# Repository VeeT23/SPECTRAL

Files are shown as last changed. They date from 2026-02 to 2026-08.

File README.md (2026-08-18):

# SPECTRAL

Short description of the embedded system and what it does.

## Overview

SPECTRAL is a performance line following robot 

## Hardware

### Main Components

| Component | Part Number | Description |
| --- | --- | --- |
| MCU | ESP32-WROOM-32UE  | Main microcontroller |
| Orientation Sensor | BNO055 | 9-DoF absolute orientation sensor with accelerometer, gyroscope, and magnetometer |
| Motor Controller | ODrive Micro | 100 W BLDC motor controller |
| Motor | Flash Hobby D4215 | 4215 650 KV BLDC motor, 3S–6S |
| CAN Transceiver | ATA6561 | CAN transceiver for motor controller communication |

### Pinout

## Pin Definitions

| GPIO | Function | Interface | Notes |
| ---: | --- | --- | --- |
| 16 | A0 | Sensor Address | Sensor address select |
| 17 | A1 | Sensor Address | Sensor address select |
| 18 | A2 | Sensor Address | Sensor address select |
| 32 | S0 | Sensor Output  | Sensor output |
| 33 | S1 | Sensor Output  | Sensor output |
| 34 | S2 | Sensor Output  | Sensor output |
| 35 | S3 | Sensor Output  | Sensor output |
| 39 | S4 | Sensor Output  | Sensor output |
| 19 | CAN_STBY | CAN | CAN transceiver standby control |
| 4 | CAN_RX | CAN | CAN receive |
| 5 | CAN_TX | CAN | CAN transmit |
| 22 | SDA | I2C | I2C data |
| 21 | SCL | I2C | I2C clock |
| 25 | BUZZER | GPIO | Buzzer control |
| 26 | NEOPIXEL | GPIO | Exposed on board; currently unused |
| 27 | FAN_PWM  | PWM | Exposed on board; currently unused |

## Software

### Toolchain

- **Platform:** Espressif32
- **MCU:** ESP32-WROOM-32UE
- **Framework:** Arduino
- **Build System:** PlatformIO
- **IDE:** Visual Studio Code + PlatformIO

## Repository Structure

```text
SPECTRAL/
├── firmware/
│   ├── common/
│   ├── control_station_firmware/
│   └── spectral_firmware/
├── hardware/
│   ├── main_board/
│   ├── power_module/
│   └── sensor_module/
├── .gitignore
└── README.md
```

## Configuration

| Parameter | Value | Description |
| --- | ---: | --- |
| Control Frequency | 1000 Hz | Main control loop frequency |
| Display Update Period | 40 ms | Period between display updates |
| Wheel Spacing | 104 mm | Distance between drive wheels |
| Wheel Diameter | 60 mm | Drive wheel diameter |
| Wheel Circumference | 0.1885 m | Calculated wheel circumference |
| Line Following Kp | 1.0 | Proportional gain |
| Line Following Ki | 0.01 | Integral gain |
| Line Following Kd | 0.01 | Derivative gain |
| Number of Sensor Modules | 5 | Number of IR sensor modules |
| Sensors per Module | 8 | Number of sensors on each module |
| Total IR Sensors | 40 | Total number of IR sensors |
| IR Threshold | 2000 | Sensor threshold used for line detection |
| Controller MAC | `D8:3B:DA:46:57:80` | MAC address of the remote controller |
| Radio RX Timeout | 1000 ms | Maximum time without receiving controller data |
| Telemetry Frequency | 120 Hz | Telemetry transmission frequency |
| Radio Debug | Disabled | Enables/disables radio debug output |
| CAN Bitrate | 500 kbit/s | CAN bus communication speed |
| CAN TX Timeout | 40 ms | Maximum time to wait for CAN transmission |
| Serial Baud Rate | 115200 | Serial communication baud rate |
| ODrive Heartbeat Timeout | 200 ms | Maximum time without receiving an ODrive heartbeat |
| Motors Enabled | Yes | Enables motor operation |

### ODrive Commands

The following CAN command IDs are used to communicate with the ODrive motor controller:

| Command | CAN ID | Description |
| --- | -----: | --- |
| Heartbeat | `0x01` | ODrive heartbeat |
| Emergency Stop | `0x02` | Trigger emergency stop |
| Set Axis State | `0x07` | Change ODrive axis state |
| Get Encoder Estimate | `0x09` | Request encoder position/velocity estimate |
| Set Input Velocity | `0x0D` | Set motor velocity command |
| Clear Errors | `0x18` | Clear ODrive errors |

### ODrive Axis States

| State | Value | Description |
| --- | ----: | --- |
| Idle | `1` | Motor disabled / idle |
| Closed Loop | `8` | Motor enabled for closed-loop control |

## Power

Spectral uses a 450 mAh 3s 75C lipo
Running power is unknown however the circuit supports up to 10A continous.
Idle power is measured to be ~140ma

WARNING: AS IT STANDS CURRENTLY, SPECTRAL LACKS OVER DISCHARGE PROTECTION, MONITOR BATTERY VOLTAGE BETWEEN RUNS TO AVOID DAMAGE TO THE BATTERY

## Communication

* UART - Serial debugging/flashing
* I2C - Display screen
* CAN - Motor controllers
* ESP-NOW - Base station communication

## Known Issues

* Dynamic velocity control has no smoothing between setpoints
* Power module lacks battery monitoring for undervoltage

## Future Work

This project is closed, however I will add documentation/clean up issues on request. 

## License

This project is licensed under the GNU GENERAL PUBLIC LICENSE.

## Author

**Veronica Tobias**

[GitHub](https://github.com/VeeT23)

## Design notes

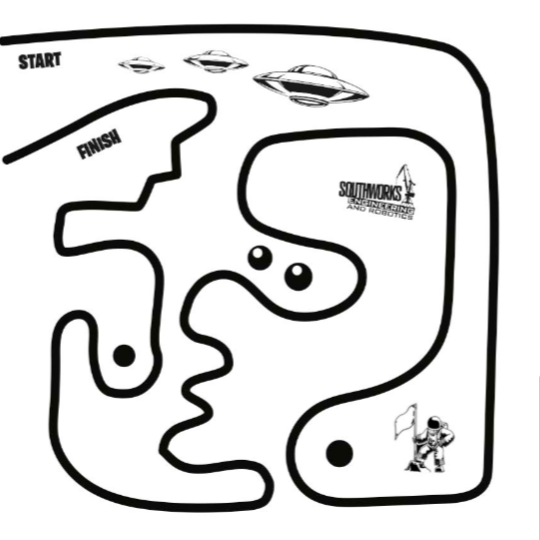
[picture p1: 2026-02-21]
spectral_data_analysis/pathfinder_2026.png

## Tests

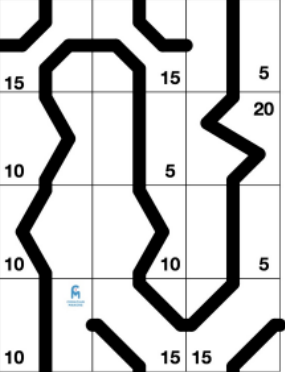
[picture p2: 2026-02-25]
spectral_data_analysis/test.png

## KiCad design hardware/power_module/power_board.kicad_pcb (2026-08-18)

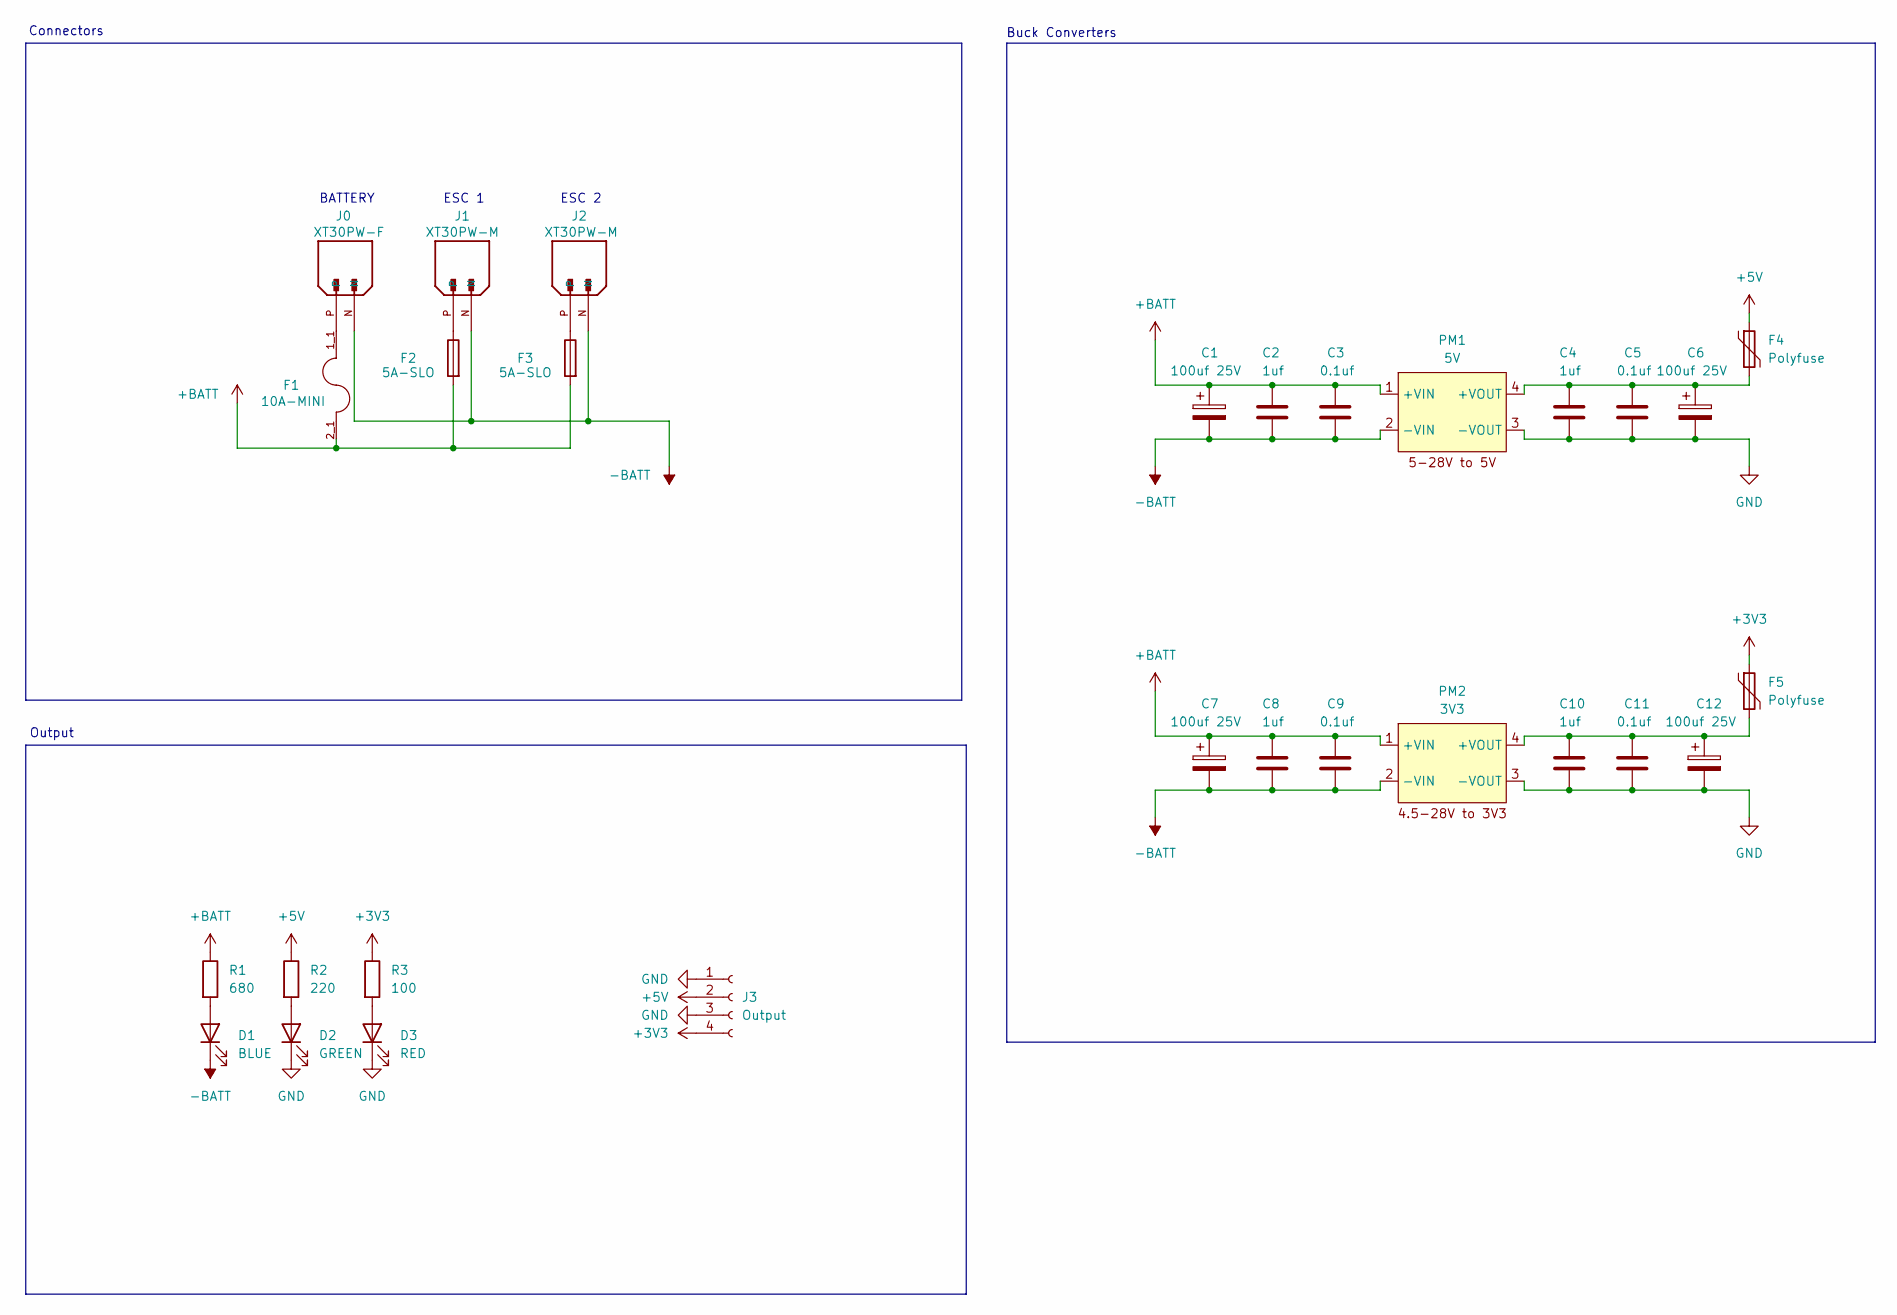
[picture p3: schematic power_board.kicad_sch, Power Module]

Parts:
C1, C6, C7, C12: 100uf 25V; CP_Radial_D5.0mm_P2.00mm
C2, C4, C8, C10: 1uf; C_0603_1608Metric_Pad1.08x0.95mm_HandSolder
C3, C5, C9, C11: 0.1uf; C_0603_1608Metric_Pad1.08x0.95mm_HandSolder
D1: BLUE; LED_0603_1608Metric_Pad1.05x0.95mm_HandSolder
D2: GREEN; LED_0603_1608Metric_Pad1.05x0.95mm_HandSolder
D3: RED; LED_0603_1608Metric_Pad1.05x0.95mm_HandSolder
F1: 10A-MINI; FUSE_3549-2; PARTREV D; DigiKey_Part_Number 36-3549-2-ND
F2, F3: 5A-SLO; Fuse_1206_3216Metric_Pad1.42x1.75mm_HandSolder
F4, F5: Polyfuse; Fuse_2920_7451Metric_Pad2.10x5.45mm_HandSolder
J0: XT30PW-F; AMASS_XT30PW-M; PARTREV 1.2
J1, J2: XT30PW-M; AMASS_XT30PW-M; PARTREV 1.2
J3: Output; JST_GH_BM04B-GHS-TBT_1x04-1MP_P1.25mm_Vertical
PM1: 5V; DC_Buck_Module
PM2: 3V3; DC_Buck_Module
R1: 680; R_0603_1608Metric_Pad0.98x0.95mm_HandSolder
R2: 220; R_0603_1608Metric_Pad0.98x0.95mm_HandSolder
R3: 100; R_0603_1608Metric_Pad0.98x0.95mm_HandSolder

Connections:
+3V3: F5.1, J3.4, R3.1
+5V: F4.1, J3.2, R2.1
+BATT: C1.1, C2.1, C3.1, C7.1, C8.1, C9.1, F1.2_1, F1.2_2, F2.2, F3.2, PM1.1 (+VIN), PM2.1 (+VIN), R1.1
-BATT: C1.2, C2.2, C3.2, C7.2, C8.2, C9.2, D1.1 (K), J0.N, J0.S1, J0.S2, J1.N, J1.S1, J1.S2, J2.N, J2.S1, J2.S2, PM1.2 (-VIN), PM2.2 (-VIN)
GND: C4.2, C5.2, C6.2, C10.2, C11.2, C12.2, D2.1 (K), D3.1 (K), J3.1, J3.3, J3.MP, PM1.3 (-VOUT), PM2.3 (-VOUT)
unnamed: D1.2 (A), R1.2
unnamed: D2.2 (A), R2.2
unnamed: D3.2 (A), R3.2
unnamed: F1.1_1, F1.1_2, J0.P
unnamed: F2.1, J1.P
unnamed: F3.1, J2.P
unnamed: C4.1, C5.1, C6.1, F4.2, PM1.4 (+VOUT)
unnamed: C10.1, C11.1, C12.1, F5.2, PM2.4 (+VOUT)

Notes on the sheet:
BATTERY
Connectors
ESC 1
ESC 2
Buck Converters
Output

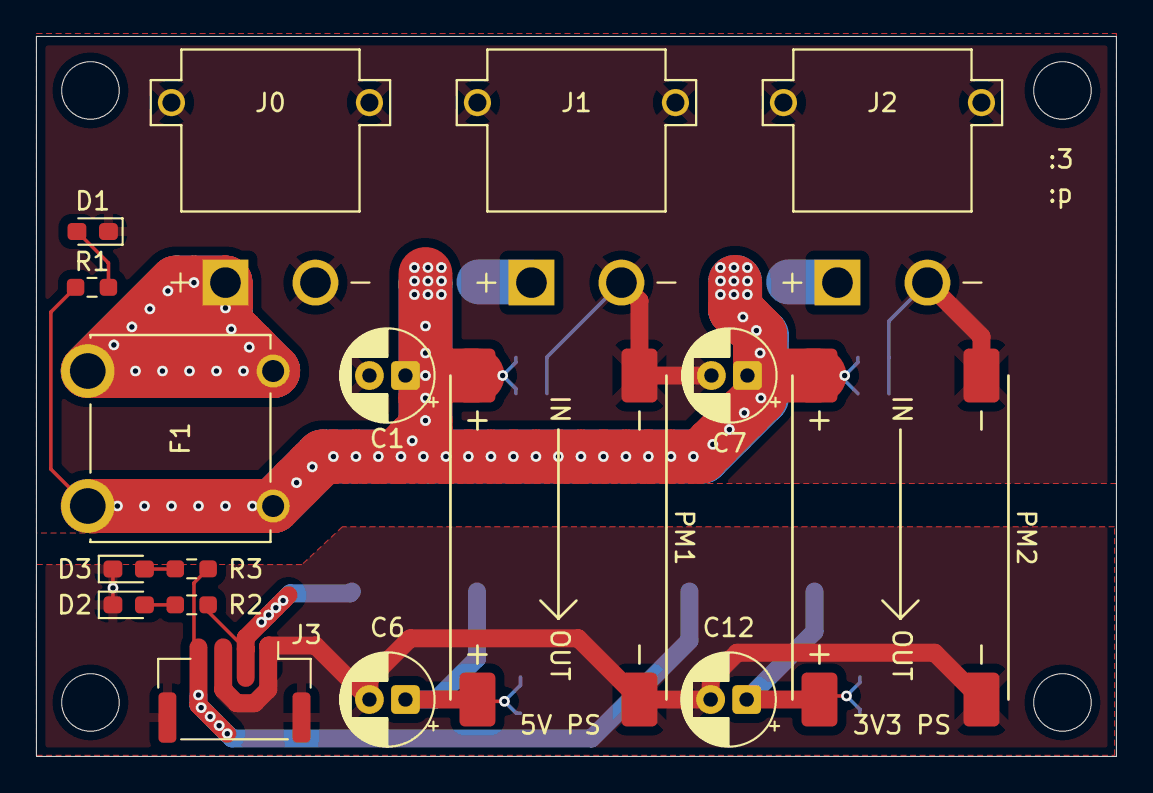
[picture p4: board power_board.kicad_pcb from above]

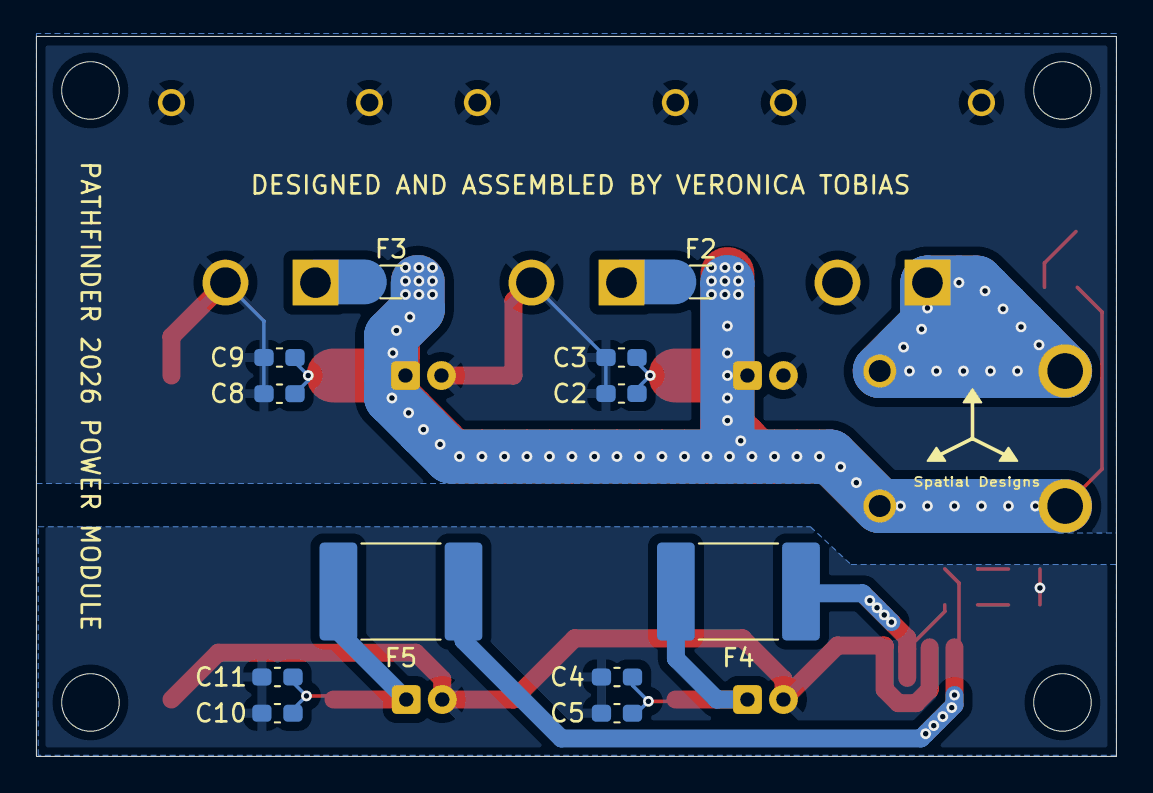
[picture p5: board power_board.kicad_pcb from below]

Board: 2 copper layers, 60.0 x 40.0 mm, 29 parts (12 on the bottom side), 13 nets.

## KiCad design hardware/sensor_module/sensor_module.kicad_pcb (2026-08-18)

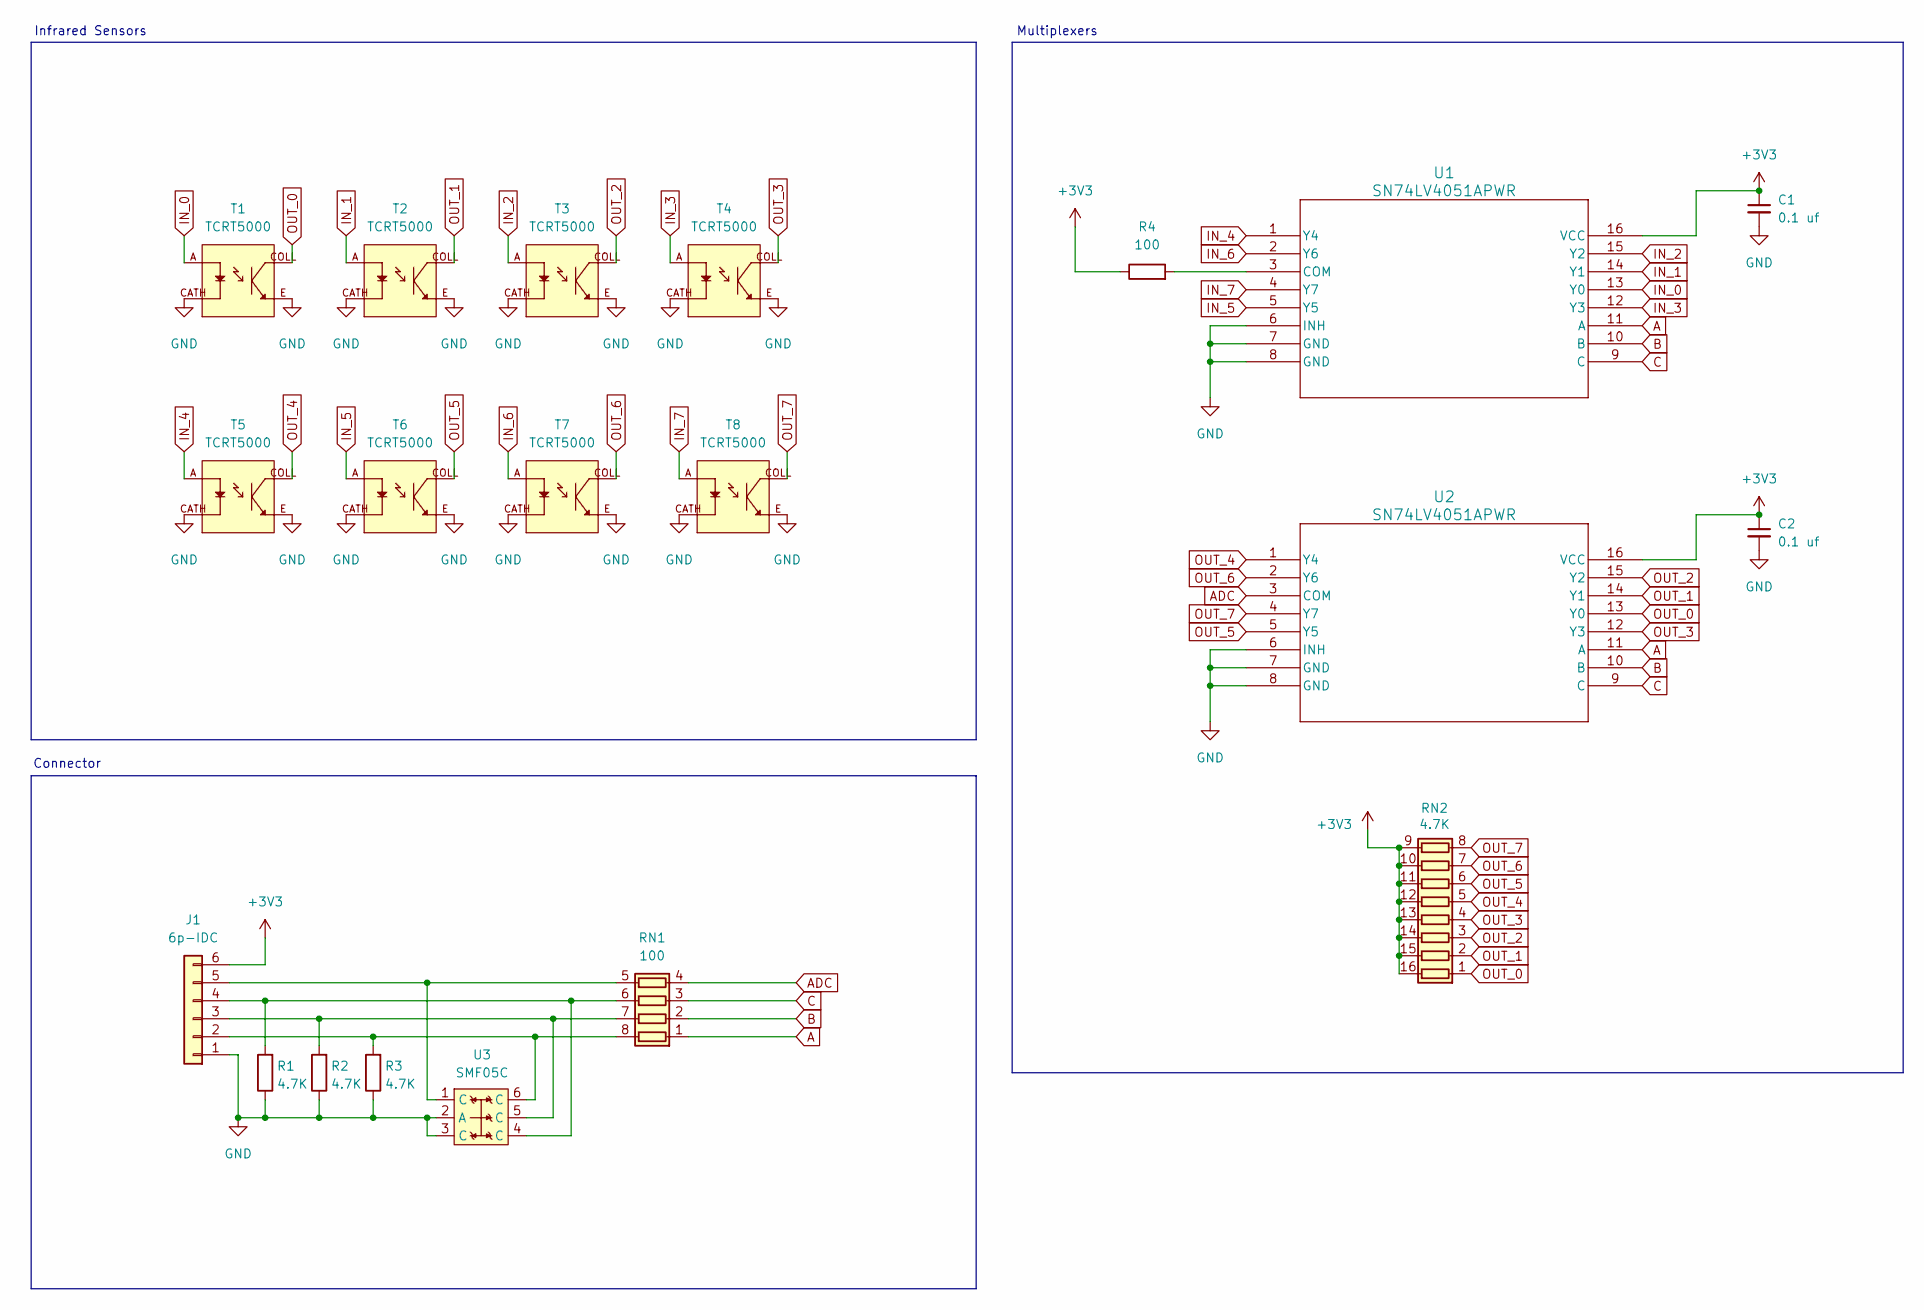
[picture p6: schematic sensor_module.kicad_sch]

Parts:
C1, C2: 0.1 uf; C_0603_1608Metric_Pad1.08x0.95mm_HandSolder
J1: 6p-IDC; CONN_SM06B-GHS-TB_JST
R1, R2, R3: 4.7K; R_0603_1608Metric_Pad0.98x0.95mm_HandSolder
R4: 100; R_0603_1608Metric_Pad0.98x0.95mm_HandSolder
RN1: 100; EXB28V_PAN-L
RN2: 4.7K; RES_EXB2HV
T1, T2, T3, T4, T5, T6, T7, T8: TCRT5000; TCRT5000-MINI; PARTREV 1.7
U1, U2: SN74LV4051APWR; PW16
U3: SMF05C; SOT-363_SC-70-6_Handsoldering

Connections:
+3V3: C1.1, C2.1, J1.6, R4.1, RN2.9 (R8.2), RN2.10 (R7.2), RN2.11 (R6.2), RN2.12 (R5.2), RN2.13 (R4.2), RN2.14 (R3.2), RN2.15 (R2.2), RN2.16 (R1.2), U1.16 (VCC), U2.16 (VCC)
A: RN1.1 (R1.1), U1.11 (A), U2.11 (A)
ADC: RN1.4 (R4.1), U2.3 (COM)
B: RN1.2 (R2.1), U1.10 (B), U2.10 (B)
C: RN1.3 (R3.1), U1.9 (C), U2.9 (C)
GND: C1.2, C2.2, J1.1, R1.1, R2.1, R3.1, T1.CATH, T1.E, T2.CATH, T2.E, T3.CATH, T3.E, T4.CATH, T4.E, T5.CATH, T5.E, T6.CATH, T6.E, T7.CATH, T7.E, T8.CATH, T8.E, U1.6 (INH), U1.7 (GND), U1.8 (GND), U2.6 (INH), U2.7 (GND), U2.8 (GND), U3.2 (A), U3.3 (C)
IN_0: T1.A, U1.13 (Y0)
IN_1: T2.A, U1.14 (Y1)
IN_2: T3.A, U1.15 (Y2)
IN_3: T4.A, U1.12 (Y3)
IN_4: T5.A, U1.1 (Y4)
IN_5: T6.A, U1.5 (Y5)
IN_6: T7.A, U1.2 (Y6)
IN_7: T8.A, U1.4 (Y7)
unnamed: J1.2, R3.2, RN1.8 (R1.2), U3.6 (C)
unnamed: J1.3, R2.2, RN1.7 (R2.2), U3.5 (C)
unnamed: J1.4, R1.2, RN1.6 (R3.2), U3.4 (C)
unnamed: J1.5, RN1.5 (R4.2), U3.1 (C)
unnamed: R4.2, U1.3 (COM)
OUT_0: RN2.1 (R1.1), T1.COLL, U2.13 (Y0)
OUT_1: RN2.2 (R2.1), T2.COLL, U2.14 (Y1)
OUT_2: RN2.3 (R3.1), T3.COLL, U2.15 (Y2)
OUT_3: RN2.4 (R4.1), T4.COLL, U2.12 (Y3)
OUT_4: RN2.5 (R5.1), T5.COLL, U2.1 (Y4)
OUT_5: RN2.6 (R6.1), T6.COLL, U2.5 (Y5)
OUT_6: RN2.7 (R7.1), T7.COLL, U2.2 (Y6)
OUT_7: RN2.8 (R8.1), T8.COLL, U2.4 (Y7)

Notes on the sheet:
Infrared Sensors
Connector
Multiplexers

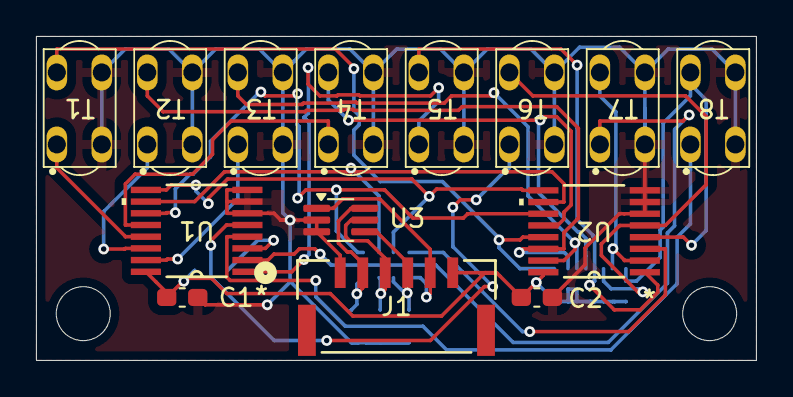
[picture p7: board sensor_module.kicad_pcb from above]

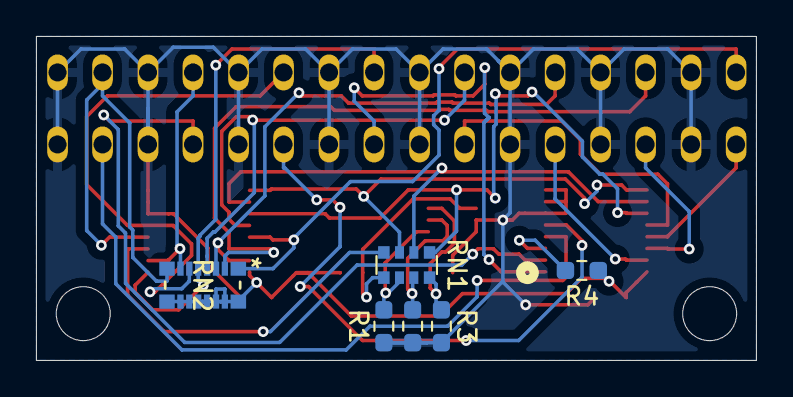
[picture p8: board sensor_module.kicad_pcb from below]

Board: 2 copper layers, 40.0 x 18.0 mm, 20 parts (6 on the bottom side), 27 nets.

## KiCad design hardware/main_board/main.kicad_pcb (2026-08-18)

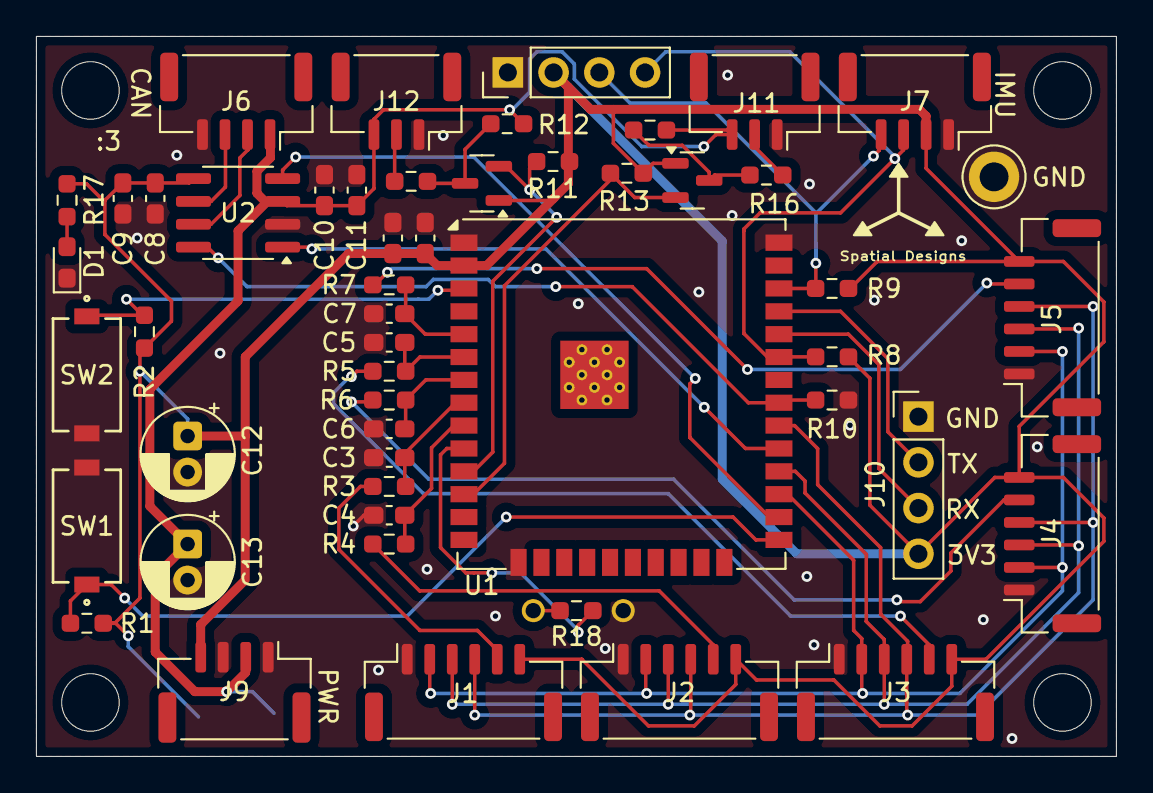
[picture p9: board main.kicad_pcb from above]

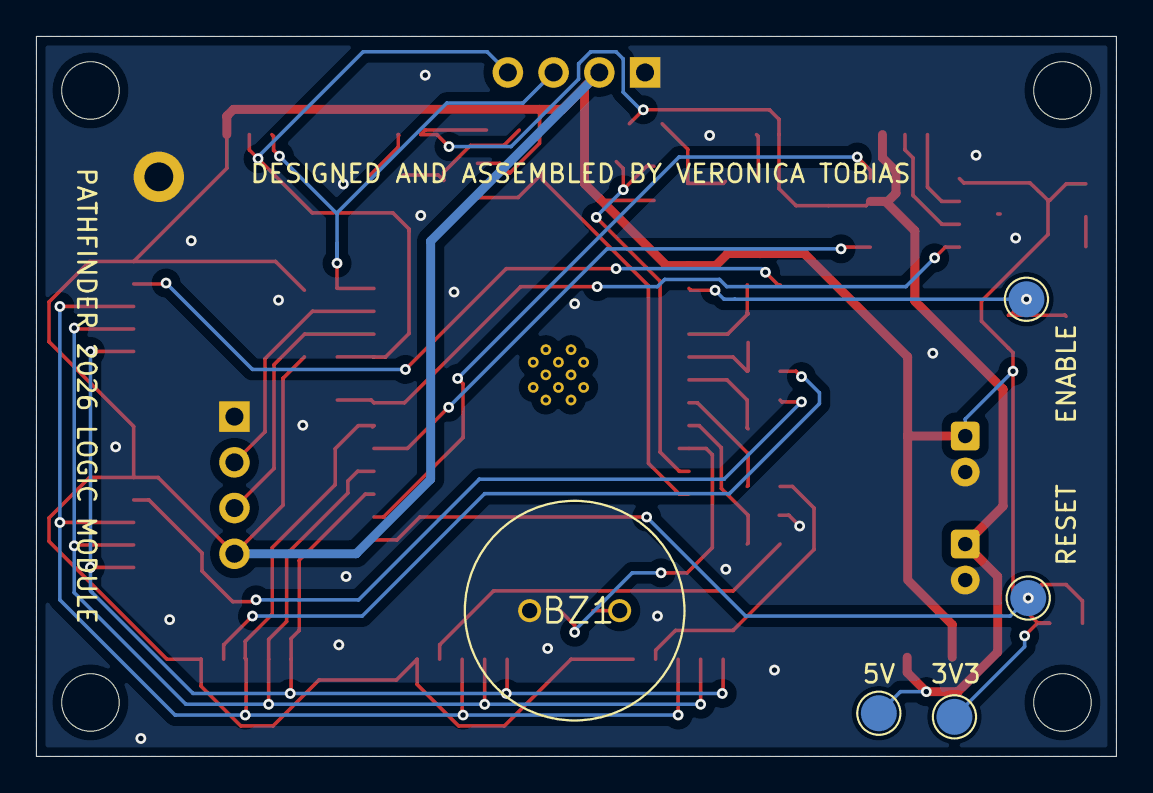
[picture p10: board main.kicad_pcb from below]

Board: 2 copper layers, 60.0 x 40.0 mm, 56 parts (5 on the bottom side), 36 nets.

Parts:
BZ1: Buzzer; XDCR_PS1240P02CT3
C1, C8, C10: 0.1uf; C_0603_1608Metric_Pad1.08x0.95mm_HandSolder
C2, C9, C11: 10uf; C_0603_1608Metric_Pad1.08x0.95mm_HandSolder
C3, C4, C5, C6, C7: 1nf; C_0603_1608Metric_Pad1.08x0.95mm_HandSolder
C12, C13: 100uf; CP_Radial_D5.0mm_P2.00mm
D1: RED; LED_0603_1608Metric_Pad1.05x0.95mm_HandSolder
J1: Sensor 1; JST_GH_SM06B-GHS-TB_1x06-1MP_P1.25mm_Horizontal
J2: Sensor 2; JST_GH_SM06B-GHS-TB_1x06-1MP_P1.25mm_Horizontal
J3: Sensor 3; JST_GH_SM06B-GHS-TB_1x06-1MP_P1.25mm_Horizontal
J4: Sensor 4; JST_GH_SM06B-GHS-TB_1x06-1MP_P1.25mm_Horizontal
J5: Sensor 5; JST_GH_SM06B-GHS-TB_1x06-1MP_P1.25mm_Horizontal
J6: CAN; JST_GH_SM04B-GHS-TB_1x04-1MP_P1.25mm_Horizontal
J7: IMU; JST_GH_SM04B-GHS-TB_1x04-1MP_P1.25mm_Horizontal
J8: OLED; PinHeader_1x04_P2.54mm_Vertical
J9: Power; JST_GH_BM04B-GHS-TBT_1x04-1MP_P1.25mm_Vertical
J10: UART; PinHeader_1x04_P2.54mm_Vertical
J11: PWM; JST_GH_SM03B-GHS-TB_1x03-1MP_P1.25mm_Horizontal
J12: NEOPIXEL; JST_GH_SM03B-GHS-TB_1x03-1MP_P1.25mm_Horizontal
Q1, Q4: BSS138; SOT-23
R1, R2, R8, R9, R10, R11, R12, R13, R14: 4.7K; R_0603_1608Metric_Pad0.98x0.95mm_HandSolder
R3, R4, R5, R6, R7, R15, R16, R17, R18: 100; R_0603_1608Metric_Pad0.98x0.95mm_HandSolder
SW1: BOOT; SW_PTS636_CNK
SW2: RESET; SW_PTS636_CNK
TP1: BOOT; TestPoint_Pad_D2.0mm
TP2: EN; TestPoint_Pad_D2.0mm
TP3: 3V3; TestPoint_Pad_D2.0mm
TP4: 5V; TestPoint_Pad_D2.0mm
TP5: GND; TestPoint_Keystone_5005-5009_Compact
U1: ESP32-WROOM-32UE_M113EH6400UH3Q0_; ESP32-WROOM-32UE
U2: ATA6561-GAQW-N; SOIC-8_3.9x4.9mm_P1.27mm

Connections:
+3V3: C1.1, C2.1, C8.1, C9.1, C12.1, J1.6, J2.6, J3.6, J4.6, J5.6, J7.2, J8.2, J9.4, J10.4, Q1.1 (G), Q4.1 (G), R1.1, R2.1, R8.2, R9.2, R11.2, R13.2, R17.1, TP3.1, U1.2 (3V3), U2.5 (VRXD)
+5V: C10.1, C11.1, C13.1, J6.1, J9.2, J11.3, J12.3, R12.2, R14.2, TP4.1, U2.3 (VCC)
A0: J1.2, J2.2, J3.2, J4.2, J5.2, U1.27 (IO16)
A1: J1.3, J2.3, J3.3, J4.3, J5.3, U1.28 (IO17)
A2: J1.4, J2.4, J3.4, J4.4, J5.4, U1.30 (IO18)
BOOT: R1.2, SW1.1, TP1.1, U1.25 (IO0)
BUZZER: R18.1, U1.10 (IO25)
CAN_RX: U1.26 (IO4), U2.4 (RXD)
CAN_STBY: R10.1, U1.31 (IO19), U2.8 (S)
CAN_TX: U1.29 (IO5), U2.1 (TXD)
EN: R2.2, SW2.1, TP2.1, U1.3 (EN)
GND: BZ1.2 (-), C1.2, C2.2, C3.2, C4.2, C5.2, C6.2, C7.2, C8.2, C9.2, C10.2, C11.2, C12.2, C13.2, D1.1 (K), J1.1, J2.1, J3.1, J4.1, J5.1, J6.4, J7.1, J8.1, J9.1, J9.3, J10.1, J11.1, J12.1, R10.2, SW1.2, SW2.2, TP5.1, U1.1 (GND), U1.15 (GND), U1.38 (GND), U2.2 (GND)
NEO: Q4.2 (S), R11.1, U1.11 (IO26)
unnamed: BZ1.1 (+), R18.2
unnamed: D1.2 (A), R17.2
unnamed: J6.2, U2.7 (CANH)
unnamed: J6.3, U2.6 (CANL)
unnamed: J11.2, R16.2
unnamed: J12.2, R15.2
unnamed: Q1.3 (D), R14.1, R16.1
unnamed: Q4.3 (D), R12.1, R15.1
unnamed: C3.1, R3.2, U1.8 (IO32)
unnamed: C4.1, R4.2, U1.9 (IO33)
unnamed: C5.1, R5.1, U1.6 (IO34)
unnamed: C6.1, R6.1, U1.7 (IO35)
unnamed: C7.1, R7.1, U1.5 (SENSOR_VN)
PWM: Q1.2 (S), R13.1, U1.12 (IO27)
RX: J10.3, U1.34 (RXD0)
S0: J1.5, R3.1
S1: J2.5, R4.1
S2: J3.5, R5.2
S3: J4.5, R6.2
S4: J5.5, R7.2
SCL: J7.4, J8.3, R9.1, U1.36 (IO22)
SDA: J7.3, J8.4, R8.1, U1.33 (IO21)
TX: J10.2, U1.35 (TXD0)

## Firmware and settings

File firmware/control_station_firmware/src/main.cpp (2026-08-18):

#include <Arduino.h>
#include <Wire.h>

#include "screen.h"
#include "joystick.h"
#include "pin_def.h"
#include "config.h"
#include "radio.h"
#include "packet.h"

// ================= INPUT DEVICES ===============

Joystick joy_left(
    PINS::JOY_LEFT::X,
    PINS::JOY_LEFT::Y,
    PINS::JOY_LEFT::BUTTON,
    true,
    false);

Joystick joy_right(
    PINS::JOY_RIGHT::X,
    PINS::JOY_RIGHT::Y,
    PINS::JOY_RIGHT::BUTTON,
    false,
    true);

// ================= RADIO =======================

using ControllerRadio = ESPNowRadio<ControlPacket, TelemetryPacket>;
ControllerRadio &radio = ControllerRadio::instance();

// ================= SETUP =======================

void setup()
{
    delay(2000);
    Serial.begin(576000);

    Wire.begin();

    Screen::instance().init(0x3C);
    if (!radio.begin(ROBOT_MAC, RX_TIMEOUT_MS, RADIO_DEBUG))
    {
        while (true)
        {
            delay(1000);
        }
    }
}

// ================= LOOP ========================

void loop()
{

    joy_left.poll();
    joy_right.poll();

    static uint32_t lastSend = 0;
    static uint8_t control_mode = 0;           // 0: IDLE, 1: MANUAL, 2: AUTO
    static float max_velocity = BASE_VELOCITY; // Default max velocity, can be adjusted in AUTO mode
    static bool in_config_menu = false;

    if (joy_left.just_released())
    {
        if (in_config_menu)
        {
            in_config_menu = false;
        }
        else
        {
            if (control_mode == 0) // Only allow config menu access from IDLE mode
            {
                in_config_menu = true;
            }
            else
            {
                control_mode = 0; // IDLE
            }
        }
    }

    if (joy_right.just_released())
    {
        if (in_config_menu)
        {
            // Exit config menu on right joystick button press
            in_config_menu = false;
        }
        else
        {
            // Cycle control modes on right joystick button press
            control_mode++;
            if (control_mode > 2)
                control_mode = 0;
        }
    }

    if (in_config_menu)
    {
        max_velocity += joy_right.y() * 0.005f;               // Adjust max velocity with right joystick up/down
        max_velocity = constrain(max_velocity, 0.05f, 10.0f); // Constrain to reasonable range
    }

    if (millis() - lastSend >= TX_PERIOD)
    {
        lastSend = millis();

        float throttle = joy_left.y() * max_velocity;                    // Forward/backward on left joystick
        float steering = joy_right.x() * (1 - abs(joy_left.y()) * 0.5f); // Left/right on right joystick

        float throttle_left, throttle_right;

        if (throttle == 0.0f && steering != 0.0f)
        {
            // In-place turning: wheels spin opposite directions
            throttle_left = steering * max_velocity;
            throttle_right = -steering * max_velocity;
        }
        else
        {
            // Normal turning: adjust throttle per wheel
            float turn_scale = steering * abs(throttle);
            throttle_left = throttle + turn_scale;
            throttle_right = throttle - turn_scale;
        }

        ControlPacket cmd{};
        cmd.control_mode = control_mode;
        cmd.throttle_left = throttle_left; // m/s
        cmd.throttle_right = throttle_right;
        cmd.max_velocity = max_velocity; // Only used in AUTO mode
        radio.send(cmd);
    }

    bool timeout = radio.update();

    TelemetryPacket pkt;

    if (radio.recieve(pkt))
    {
        if (Serial)
        {
            const uint16_t size = sizeof(pkt);

            Serial.write((uint8_t *)&TELEMETRY_HEADER, sizeof(TELEMETRY_HEADER));
            Serial.write((uint8_t *)&size, sizeof(size));
            Serial.write((uint8_t *)&pkt, size);
        }
    }

    // ---- UI ----
    auto &gfx = Screen::instance().gfx();
    gfx.clearDisplay();

    if (in_config_menu)
    {
        gfx.setTextSize(1);
        gfx.setCursor(0, 0);
        gfx.printf("Max Velocity: %.2f", max_velocity);
    }
    else
    {                // Default control menu
        if (timeout) // Prioritize showing timeout error over no serial error, since no serial may just mean "not plugged in yet"
        {
            Screen::instance().drawCenteredText("TIMEOUT", 0, 0, 128, 32, 2);
        }
        else
        {
            if (!Serial)
            {
                Screen::instance().drawCenteredText("NO SERIAL", 0, 0, 128, 32, 1);
            }
        }

        joy_left.draw(0, 32, 32, 32);
        joy_right.draw(96, 32, 32, 32);

        // Draw MODE label in top center box
        Screen::instance().drawCenteredText("MODE", 32, 32, 64, 16, 1);

        // Draw control mode value in bottom center box
        const char *mode_str = "";
        switch (control_mode)
        {
        case 0:
            mode_str = "IDLE";
            break;
        case 1:
            mode_str = "REMO";
            break;
        case 2:
            mode_str = "AUTO";
            break;
        }
        Screen::instance().drawCenteredText(mode_str, 32, 48, 64, 16, 2);
    }
    gfx.display();
    delay(10);
}

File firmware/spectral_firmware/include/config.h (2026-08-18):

#pragma once
#include <Arduino.h>

// ---------------- CONTROL ----------------
constexpr uint32_t CONTROL_HZ = 1000;
constexpr TickType_t CONTROL_PERIOD = pdMS_TO_TICKS(1000 / CONTROL_HZ);
constexpr TickType_t DRAW_PERIOD = pdMS_TO_TICKS(40);

constexpr uint8_t WHEEL_SPACING_MM = 104;
constexpr uint8_t WHEEL_DIAMETER_MM = 60;
constexpr float WHEEL_SPACING_M = WHEEL_SPACING_MM / 1000.0f;
constexpr float WHEEL_CIRCUMFERENCE_M =
    (WHEEL_DIAMETER_MM * PI) / 1000.0f;

constexpr float KP = 1.0f;  // Proportional gain for line following
constexpr float KI = 0.01f; // Integral gain for line following
constexpr float KD = 0.01f; // Derivative gain for line following

// ---------------- IR SENSORS ----------------
constexpr uint8_t NUM_MODULES = 5;
constexpr uint8_t SENSORS_PER_MODULE = 8;
constexpr uint8_t TOTAL_SENSORS = NUM_MODULES * SENSORS_PER_MODULE;
constexpr uint16_t IR_THRESHOLD = 2000; // Example threshold value

// ---------------- RADIO ----------------

const uint8_t CONTROLLER_MAC[6] = {0xD8, 0x3B, 0xDA, 0x46, 0x57, 0x80};
constexpr uint32_t RX_TIMEOUT_MS = 1000;
constexpr uint32_t TELEMETRY_FREQUENCY_HZ = 120;
constexpr TickType_t TELEMETRY_PERIOD = pdMS_TO_TICKS(1000 / TELEMETRY_FREQUENCY_HZ);
constexpr bool RADIO_DEBUG = false;

// ---------------- CAN ----------------
constexpr uint32_t CAN_BITRATE = 500000;
constexpr uint32_t CAN_TX_TIMEOUT_MS = 40;

// ---------------- SERIAL ----------------
constexpr uint32_t SERIAL_BAUD = 115200;

// ---------------- ODRIVE ----------------
constexpr uint32_t ODRIVE_CMD_HEARTBEAT = 0x01;
constexpr uint32_t ODRIVE_CMD_ESTOP = 0x02;
constexpr uint32_t ODRIVE_CMD_SET_AXIS_STATE = 0x07;
constexpr uint32_t ODRIVE_CMD_GET_ENCODER_EST = 0x09;
constexpr uint32_t ODRIVE_CMD_SET_INPUT_VEL = 0x0D;
constexpr uint32_t ODRIVE_CMD_CLEAR_ERRORS = 0x18;

constexpr uint32_t AXIS_STATE_CLOSED_LOOP = 8;
constexpr uint32_t AXIS_STATE_IDLE = 1;

constexpr uint32_t HEARTBEAT_TIMEOUT_MS = 200;

// ---------------- DEBUG ----------------
constexpr bool ENABLE_MOTORS = true;

// See radio for RADIO_DEBUG

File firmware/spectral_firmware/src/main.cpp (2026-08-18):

#include <Arduino.h>
#include "pin_def.h" // Pin configs
// Debug
#include "screen.h"
#include "buzzer.h"
// Peripherals
#include "global_state.h" //Holds radio + global data
#include "can_bus.h"
// Main loop
#include "control.h"

#include "splash.h"

/**
 * Main boot sequence
 * see global_state.h for config
 */

void setup()
{
    delay(100);
    // ---------- SERIAL INIT ----------
    Serial.begin(SERIAL_BAUD);
    Serial.println("Booting...");


    // ---------- CONFIGURE PINS ---------
    Serial.println("Configuring Pins...");
    PINS::configure_pins();
    

    // ---------- I2C INIT ----------
    Serial.println("Initializing I2C...");
    Wire.begin(PINS::SDA, PINS::SCL);
    Wire.setClock(400000);
    Wire.setTimeOut(5);

    // ---------- SCREEN INIT ----------
    Serial.println("Initializing OLED...");
    Screen::instance().init(0x3C);
    Screen::instance().gfx().clearDisplay();
    Screen::instance().gfx().drawBitmap(0, 0, SPLASH, 128, 64, SSD1306_WHITE);
    Screen::instance().gfx().display();

    // ---------- RADIO INIT ----------
    Serial.println("Initializing Radio...");
    auto& radio = RadioInstance();
    if (!radio.begin(CONTROLLER_MAC, RX_TIMEOUT_MS, RADIO_DEBUG)) {
        Serial.println("Radio init failed!");
        while (true) { delay(1000); }
    }

    // ---------- CAN INIT ----------
    Serial.println("Initializing CAN Bus...");
    if (!CANBus::instance().begin(PINS::CAN_TX, PINS::CAN_RX, CAN_BITRATE))
    {
        Serial.println("CAN init failed!");
        while (true) { delay(1000); }
    }
    if (CANBus::instance().test_can())
    {
        Serial.println("CAN TX failed!");
        while (true) { delay(1000); }
    }
    // ---------- BOOT FINISH ----------
    Serial.println("Boot sequence complete!");
    Buzzer::beep(2000,100);
    delay(2000);
    setup_control();
}

void loop()
{
    vTaskDelay(portMAX_DELAY);
}

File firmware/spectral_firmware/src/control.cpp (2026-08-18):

#include "control.h"
#include "pin_def.h"
#include "motor.h"
#include "screen.h"
#include "global_state.h"
#include "config.h"
#include "sensor_array.h"
#include "gyro.h"
#include "solution.h"

struct OdometryState
{
    float x = 0.0f;     // meters
    float y = 0.0f;     // meters
    float theta = 0.0f; // radians

    float distance = 0.0f; // total arc length traveled (meters)

    float prev_rev_L = 0.0f;
    float prev_rev_R = 0.0f;
};

inline void updateOdometry(
    OdometryState &state,
    float current_rev_L,
    float current_rev_R)
{
    // ---- Compute delta revolutions ----
    float delta_rev_L = current_rev_L - state.prev_rev_L;
    float delta_rev_R = current_rev_R - state.prev_rev_R;

    if (fabs(delta_rev_L) > 5 || fabs(delta_rev_R) > 5)
    {
        delta_rev_L = 0;
        delta_rev_R = 0;
    }

    state.prev_rev_L = current_rev_L;
    state.prev_rev_R = current_rev_R;

    // ---- Convert revolutions -> linear distance (meters) ----
    float dL = delta_rev_L * WHEEL_CIRCUMFERENCE_M;
    float dR = delta_rev_R * WHEEL_CIRCUMFERENCE_M;

    // ---- Differential drive kinematics ----
    float d = 0.5f * (dL + dR);                 // forward arc length

    // Accumulate arc length for distance traveled
    state.distance += d;
}

inline float wrapDegrees180(float angle_deg)
{
    while (angle_deg > 180.0f)
    {
        angle_deg -= 360.0f;
    }

    while (angle_deg <= -180.0f)
    {
        angle_deg += 360.0f;
    }

    return angle_deg;
}

inline float unwrapAngleNearReference(float angle_deg, float reference_deg)
{
    return reference_deg + wrapDegrees180(angle_deg - reference_deg);
}

inline bool hasReachedSolutionAngle(float previous_angle_deg, float target_angle_deg, float heading_deg)
{
    const float previous_unwrapped = unwrapAngleNearReference(previous_angle_deg, heading_deg);
    const float target_unwrapped = unwrapAngleNearReference(target_angle_deg, previous_unwrapped);

    if (target_unwrapped > previous_unwrapped)
    {
        return heading_deg >= target_unwrapped;
    }

    if (target_unwrapped < previous_unwrapped)
    {
        return heading_deg <= target_unwrapped;
    }

    return true;
}

inline bool isDistanceInSpan(float distance_m, const SolutionSpan &span)
{
    const float span_start = (span.start_distance < span.end_distance) ? span.start_distance : span.end_distance;
    const float span_end = (span.start_distance < span.end_distance) ? span.end_distance : span.start_distance;
    return distance_m >= span_start && distance_m <= span_end;
}

inline float getSpanPercentVelocityForDistance(const std::vector<SolutionSpan> &spans, float distance_m)
{
    for (size_t i = 0; i < spans.size(); ++i)
    {
        if (isDistanceInSpan(distance_m, spans[i]))
        {
            return spans[i].percent_velocity;
        }
    }

    return 1.0f;
}

inline void printSolutionDeserializeFailure(const char *label, const SolutionDeserializeDebugInfo &debug_info)
{
    Serial.printf(
        "Failed to decode %s: %s\n",
        label,
        solutionDeserializeErrorToString(debug_info.error));
    Serial.printf(
        "  data_len=%lu expected_len=%lu count=%lu failed_index=%lu\n",
        static_cast<unsigned long>(debug_info.data_length),
        static_cast<unsigned long>(debug_info.expected_length),
        static_cast<unsigned long>(debug_info.element_count),
        static_cast<unsigned long>(debug_info.failed_index));
    Serial.printf(
        "  magic=0x%08lX expected_magic=0x%08lX version=%lu expected_version=%lu\n",
        static_cast<unsigned long>(debug_info.actual_magic),
        static_cast<unsigned long>(debug_info.expected_magic),
        static_cast<unsigned long>(debug_info.actual_version),
        static_cast<unsigned long>(debug_info.expected_version));
}

inline void printDecodedSolutionSpans(const std::vector<SolutionSpan> &spans)
{
    Serial.println("Decoded solution spans:");
    for (size_t i = 0; i < spans.size(); ++i)
    {
        const SolutionSpan &span = spans[i];
        Serial.printf(
            "  [%u] start=%.3f end=%.3f speed=%.3f\n",
            static_cast<unsigned>(i),
            span.start_distance,
            span.end_distance,
            span.percent_velocity);
    }
}

// If odometry distance has exceeded a target point distance by this percent,
// we skip that target and jump to the next one.
constexpr float kSolutionDistanceJumpPercent = 1.0f;
constexpr float kMinLineFollowVelocityMps = 0.50f;

void controlTask(void *arg)
{
    // ---------- Task Scheduling -----------
    TickType_t lastWake = xTaskGetTickCount();
    TickType_t lastTelemetry = lastWake;
    TickType_t lastDraw = lastWake;
    TickType_t lastIdle = lastWake;
    TickType_t lastGyro = lastWake;
    TickType_t activeDuration = 0;
    
    // Gyro polling at 20Hz = 50ms period (reduced from 100Hz to avoid blocking)
    const TickType_t GYRO_PERIOD = pdMS_TO_TICKS(50);
    float gyro_yaw = 0.0f;
    float last_gyro_yaw = 0.0f;
    float relative_heading = 0.0f;
    bool has_gyro_yaw_sample = false;

    // ---------- Load Solution Points ----------
    std::vector<SolutionPoint> solution_points;
    std::vector<SolutionSpan> solution_spans;
    SolutionDeserializeDebugInfo point_decode_debug{};
    SolutionDeserializeDebugInfo span_decode_debug{};
    const bool points_loaded = deserializeEmbeddedSolutionPoints(solution_points, &point_decode_debug);
    const bool spans_loaded = deserializeEmbeddedSolutionSpans(solution_spans, &span_decode_debug);
    size_t next_solution_point_idx = 0;

    if (!points_loaded)
    {
        printSolutionDeserializeFailure("solution points", point_decode_debug);
        Serial.println("No valid solution points loaded; distance recalibration disabled");
    }
    else if (solution_points.empty())
    {
        Serial.println("Loaded solution points payload, but point count is 0; distance recalibration disabled");
    }
    else
    {
        relative_heading = solution_points.front().angle;
        next_solution_point_idx = (solution_points.size() > 1) ? 1 : solution_points.size();
        Serial.printf(
            "Loaded %u solution points; initial heading set to %.2f deg\n",
            static_cast<unsigned>(solution_points.size()),
            relative_heading);
    }

    if (!spans_loaded)
    {
        printSolutionDeserializeFailure("solution spans", span_decode_debug);
        Serial.println("No valid solution spans loaded; dynamic velocity scaling disabled");
    }
    else if (solution_spans.empty())
    {
        Serial.println("Loaded solution spans payload, but span count is 0; dynamic velocity scaling disabled");
    }
    else
    {
        Serial.printf(
            "Loaded %u solution spans for dynamic velocity scaling\n",
            static_cast<unsigned>(solution_spans.size()));
        printDecodedSolutionSpans(solution_spans);
    }

    // ---------- Initialize Gyro ----------
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

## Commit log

2026-01-21 Initial project structure and core modules
    Add core source, include, and configuration files for Control_hub and Logic_Module, including joystick, screen, radio, and packet abstractions. Remove obsolete OTA and receiver code. Update pin defin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
2026-02-16 Update hardware configs and improve motor/sensor control
    Apply hardware and platform updates (board, upload ports, MACs, pin mappings) and significantly improve motor telemetry, encoder handling, IR processing, and control logic. Key changes:
    - Control_hub: changed ROBOT_MAC, remapped joystick pins to analog (A0..A3), switched platformio board to seeed_xiao_esp32s3 and added upload_port, added serial log when sending commands.
    - Logic_Module config: reduced draw period, added wheel diameter/circumference, MAX_VELOCITY and MAX_REV, updated CONTROLLER_MAC and increased CAN_TX_TIMEOUT.
    - Motor class: track encoder reception, apply inversion/position offset, add zeroPosition() and waitForEncoder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
2026-02-21 Refactor telemetry, add visualizer & odometry
    Introduce end-to-end telemetry changes and tooling:
    - Common: expand ControlPacket/TelemetryPacket in Common/include/packet.h (control_mode, per-wheel throttles, ticks_since_idle, packed IR bitfield, line/pid/distance/pose fields).
    - Control hub: improve Joystick (deadzone, just_released, drawing tweaks), change Controller main to support control modes (IDLE/MANUAL/AUTO), send control_mode + per-wheel throttle, emit framed telemetry over serial (header + size + payload) and increase serial baud. Minor formatting/consistency fixes.
    - Data_Visualizer: add a new Python visualizer (gui.py, myserial.py, packet.py, main.py) and assets to read framed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
    [config.h, control.cpp, joystick.h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]
2026-02-22 Refactor GUI and extract image/path modules
    Split and refactor the app: add a new gui.py with menu and central widget builders, extract image pipeline into Arc/path_processor.py, and rename pathfinder to path_finder with new helpers. main.py now wires up make_menu/make_central_widgets and calls process_image(path) from the new module, initializes UI state, and manages stage/epsilon controls. Path drawing was enhanced to support multiple segment modes (solid, curvature, arc length), use matplotlib colormaps, and draw gradient-colored segments; compute_relative_angles was replaced by compute_segment_lengths and compute_curvature. Also added compiled .pyc files for the new modules.
2026-03-07 color_line and stages control
2026-03-09 added ir sensor widget
2026-04-15 Add telemetry DB, UI widgets and controller updates
    Large refactor and feature additions across controller firmware and data-analysis UI:
    - Common: add max_velocity to ControlPacket and drawCenteredText helper in Screen.
    - Control station firmware: introduce BASE_VELOCITY and TELEMETRY_HEADER in config; enhance joystick drawing to respect box size and constrain dot to circle; add in-config menu to tune max_velocity, 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
    - ESP32Serial (spectral_data_analysis): move to background threads with a small packe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
2026-04-15 refactor sensor array
    better code encapsulation
    better line detection
    cool beans
